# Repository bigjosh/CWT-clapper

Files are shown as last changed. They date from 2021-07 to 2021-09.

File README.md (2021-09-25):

# CWT-CLAPPER firmware, 2021 josh.com


## The mission

Be able to synchonise the clapping of the clappers, which requires sensing when the local clapper last clapped so that it can be positioned for the next clap. This is complicated becuase the only intentional sensor on board is a microphone and it is hard to differentiate beween the sound of a local clap and a nearby clap. 

## Theory of operation 

 1. As the cam rotates and pushes the blade, the spring is progessively streched. 
 2. The farther the spring is streched, the harder it is to strech it further (googgle "Hooke's law"). 
 3. The more force it takes to turn the motor, the more current it uses. 
 4. The more current the motor uses, the lower the voltage across the batteries becomes (google "internal resistance"). 
 5. We can indirectly measure the voltage across the battery with the internal ADC (https://wp.josh.com/2014/11/06/battery-fuel-guage-with-zero-parts-and-zero-pins-on-avr/)
 
 Q.E.D.: We can (sort of, barely, sextuple indirectly) measure the position of the blade by measuring the internal voltage 
 bandgap of the chip using the ADC!
  
 In practice, the change in ADC readings between the blade being fully open and fully shut is very small 
 and there is lots of noise also in these readings.
 
 So we aim to detect the most abupt change in that signal - the moment when the blade claps and the motor goes from pushing 
 a fully streched to spring to not pushing on the blade at all (there is a bit of a dead zone after a clap before the cam
 touches the blade again).
  
 To find this edge, we both filter out high freqnecy noise and amplify the longer running signal by taking periodic ADC samples 
 and summing these over a longer window. We have two consecutive windows, so when we get to the moment where one window is
 filled with samples from before the flap and the other is filled with samples from after the clap, there should be enough SNR to detect
 that by comparing the sums of all the values in each window. 
 
## Demo 
 
See them clap hare....
https://www.youtube.com/watch?v=MOf7x3NkilU&lc=UgzuyXRK9PwrqrHehkx4AaABAg.9SaJbr_eWT19Sc9pGRepJp

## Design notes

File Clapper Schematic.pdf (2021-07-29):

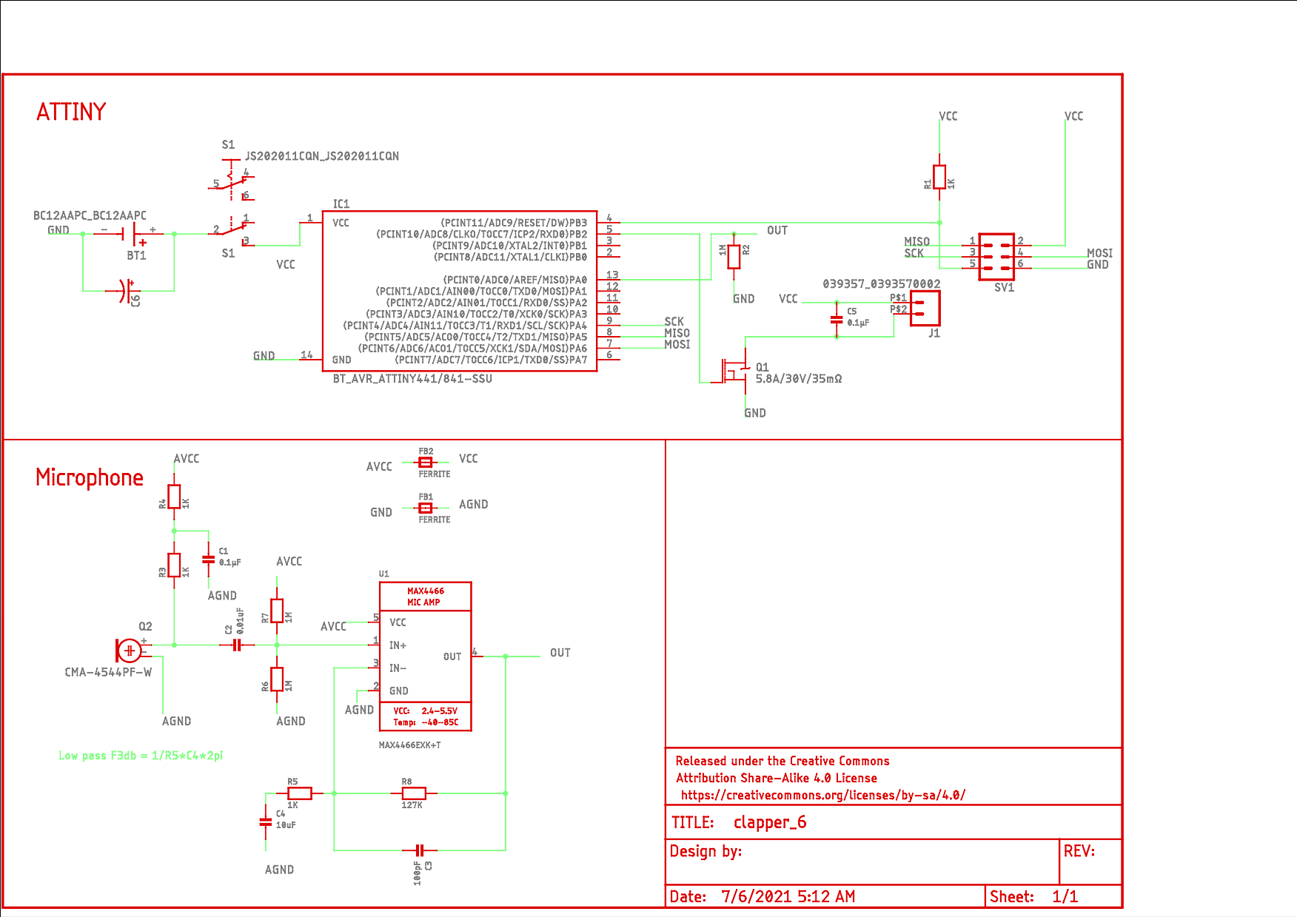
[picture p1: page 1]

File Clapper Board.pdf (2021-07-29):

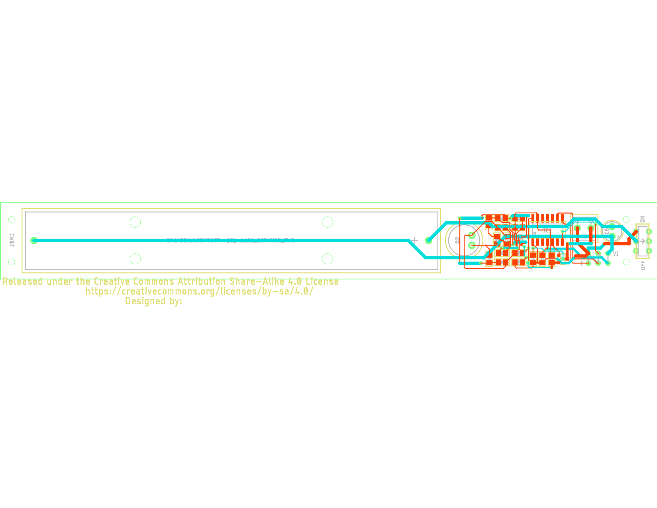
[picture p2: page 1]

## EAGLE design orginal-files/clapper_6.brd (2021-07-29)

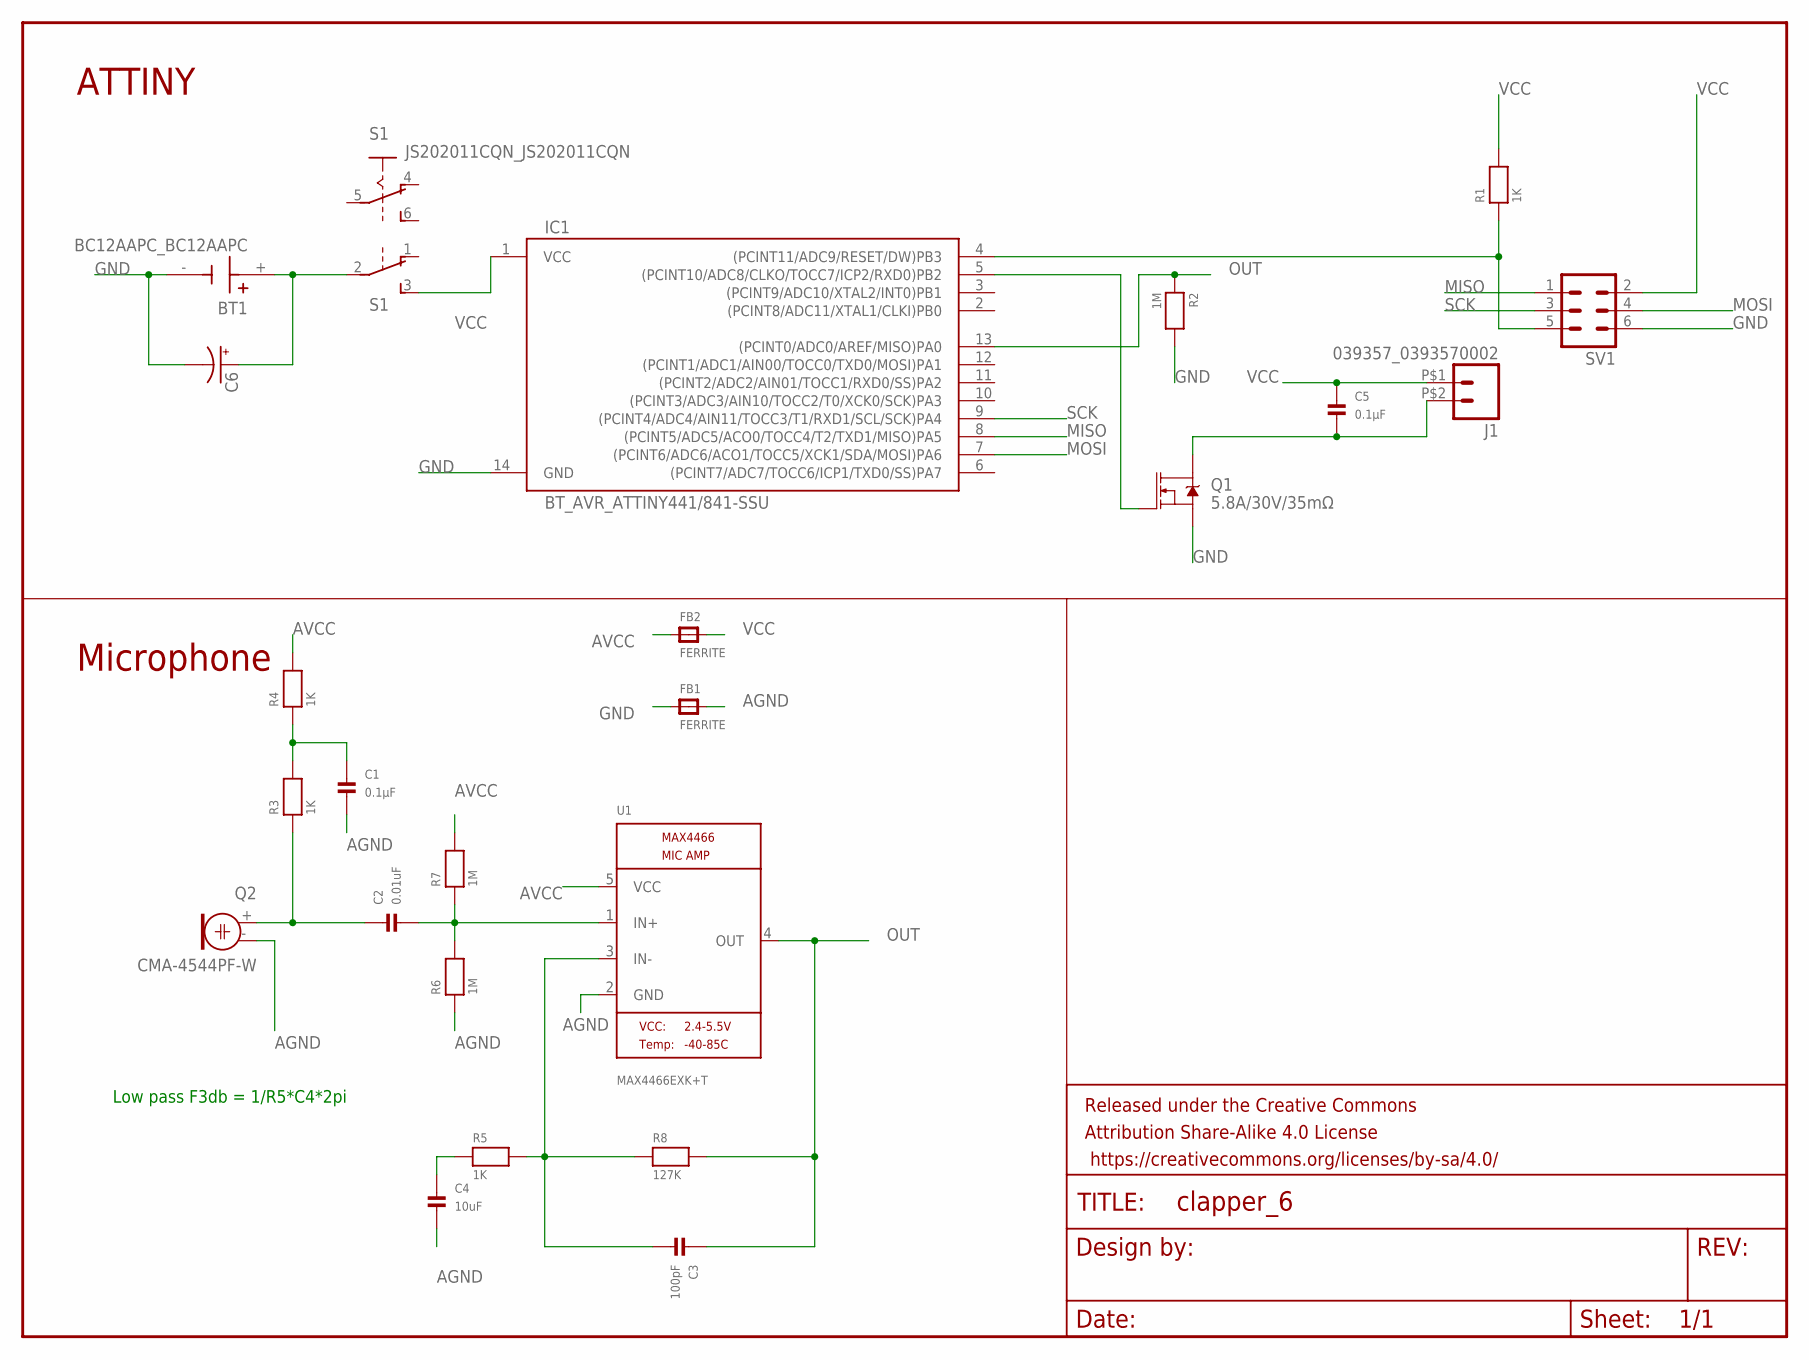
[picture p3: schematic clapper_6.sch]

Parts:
BT1: BC12AAPC_BC12AAPC; BC12AAPC_BAT_BC12AAPC
C1, C5: 0.1µF; MICROBUILDER_0805
C2: 0.01uF; MICROBUILDER_0805
C3: 100pF; MICROBUILDER_0805
C4: 10uF; MICROBUILDER_0805
C6: CPOL-USE2.5-6; E2,5-6
FB1, FB2: FERRITE; MICROBUILDER_0805
FRAME2: FRAME-LETTER; CREATIVE_COMMONS
IC1: BT_AVR_ATTINY441/841-SSU; BT_AVR_SOIC14N
J1: 039357_0393570002
Q1: 5.8A/30V/35mΩ; SOT23-3
Q2: CMA-4544PF-W; MICROBUILDER_ELECTRET_9.7
R1, R3, R4, R5: 1K; MICROBUILDER_0805
R2, R6, R7: 1M; MICROBUILDER_0805
R8: 127K; MICROBUILDER_0805
S1: JS202011CQN_JS202011CQN
SV1: CWT_MA03-2
U1: MAX4466EXK+T; MICROBUILDER_SC70-5

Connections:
AGND: C1.2, C4.2, FB1.2, Q2.- (1), R6.1, U1.2 (GND)
AVCC: FB2.1, R4.2, R7.2, U1.5 (VCC)
GND: BT1.-, C6.-, FB1.1, IC1.14 (GND), Q1.2 (S), R2.2, SV1.6
MISO: IC1.8 ((PCINT5/ADC5/ACO0/TOCC4/T2/TXD1/MISO)PA5), SV1.1
MOSI: IC1.7 ((PCINT6/ADC6/ACO1/TOCC5/XCK1/SDA/MOSI)P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), SV1.4
unnamed: C5.2, J1.P$2 (2), Q1.3 (D)
unnamed: BT1.+, C6.+, S1.2
unnamed: IC1.4 ((PCINT11/ADC9/RESET/DW)PB3), R1.1, SV1.5
unnamed: IC1.5 ((PCINT10/ADC8/CLKO/TOCC7/ICP2/RXD0)PB2), Q1.1 (G)
unnamed: C2.1, Q2.+ (2), R3.1
unnamed: C1.1, R3.2, R4.1
unnamed: C2.2, R6.2, R7.1, U1.1 (IN+)
unnamed: C3.2, R5.2, R8.1, U1.3 (IN-)
unnamed: C4.1, R5.1
OUT: C3.1, IC1.13 ((PCINT0/ADC0/AREF/MISO)PA0), R2.1, R8.2, U1.4 (OUT)
SCK: IC1.9 ((PCINT4/ADC4/AIN11/TOCC3/T1/RXD1/SCL/SC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), SV1.3
VCC: C5.1, FB2.2, IC1.1 (VCC), J1.P$1 (1), R1.2, S1.3 (S), SV1.2

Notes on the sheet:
Low pass F3db = 1/R5*C4*2pi
ATTINY
Microphone

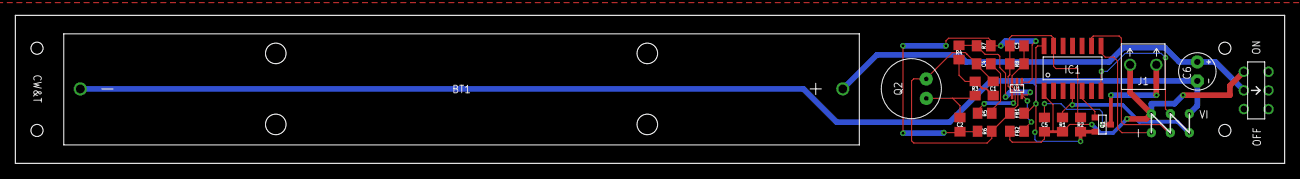
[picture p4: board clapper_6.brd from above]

Board: 2 copper layers, 169.8 x 19.8 mm, 25 parts (0 on the bottom side), 17 nets.

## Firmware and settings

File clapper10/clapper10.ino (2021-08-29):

/*
 * CWT-CLAPPER firmware, 2021 josh.com, https://github.com/bigjosh/CWT-clapper
 * 
 * Theory of operation 
 * ===================
 * 1. As the cam rotates and pushes the blade, the spring is progessively streched. 
 * 2. The farther the spring is streched, the harder it is to strech it further (googgle "Hooke's law"). 
 * 3. The more force it takes to turn the motor, the more current it uses. 
 * 4. The more current the motor uses, the lower the voltage across the batteries becomes (google "internal resistance"). 
 * 5. We can indirectly measure the voltage across the battery with the internal ADC (https://wp.josh.com/2014/11/06/battery-fuel-guage-with-zero-parts-and-zero-pins-on-avr/)
 * 
 * Q.E.D.: We can (sort of, barely, sextuple indirectly) measure the position of the blade by measuring the internal voltage 
 * bandgap of the chip using the ADC!
 * 
 * In practice, the change in ADC readings between the blade being fully open and fully shut is very small 
 * and there is lots of noise also in these readings.
 * 
 * So we aim to detect the most abupt change in that signal - the moment when the blade claps and the motor goes from pushing 
 * a fully streched to spring to not pushing on the blade at all (there is a bit of a dead zone after a clap before the cam
 * touches the blade again).
 * 
 * To find this edge, we both filter out high freqnecy noise and amplify the longer running signal by taking periodic ADC samples 
 * and summing these over a longer window. We have two consecutive windows, so when we get to the moment where one window is
 * filled with samples from before the flap and the other is filled with samples from after the clap, there should be enough SNR to detect
 * that by comparing the sums of all the values in each window. 
 */


// TO COMPLILE AND DOWNLOAD:
//  In Prefs, add to Additional Board URLs: http://drazzy.com/package_drazzy.com_index.json
//  In Board Manager, add: ATTinyCore boards
//  In Tools->Boards menu, select...
//   Board        ->attiny 441/481 (no bootloader)
//   Chip         ->attiny441
//   Clock Source ->8mhz internal <4.5V.
//   Millis       ->Enabled
//   (other stuff doesn't matter)

// After you do this, you should do "Burn Bootloader" at least one time on each chip to set the fuses to the above settings.

#include <avr/pgmspace.h>     // Almost no RAM on this chip, so we keep all strings in flash with `F()`
#include <limits.h>             // Get UNINT_MAX

// Note that all times are in milliseconds

typedef unsigned long millis_t;

// All #defines that start with MOTOR_ concern finding the notch on the cam using the motor current
// All #defines that start with MIC_   concern finding a loud trigger sound using the microphone
// Note that these two kinds of finding are completely independant of each other and only one or the other
// can be happening at any given time. This is good becuase both use the ADC, and we only have one ADC to go around. 

// Number of samples in a window (the are two windows - before- and after-clap)
// More samples mean better filtering and more amplifcation of the small changes, but bigger also means it takes more
// samples (and therefore more time) to detect a change. More samples also needs more memory, which we have very little of. 
const byte MOTOR_WINDOW_SIZE=100;     

// Time between samples. Shorter would be great, but then we would need more memory. The optimal value captures the full drop 
// within one window. Emperically this seems to be about 400ms.
const byte MOTOR_WINDOW_TIME=4;       // Time between samples

// This sets how much the 1st window accumulator must be lower than the 2nd to detect a clap.
// This depends on how much the value changes between pre- and post-clap (very little) times the number of samples in each window.
// Lower values can detect a clap more quickly, but can also lead to false positives. 

const unsigned MOTOR_THRESHOLD=75;

// Number of samples in the mic window looking for loud sounds.
// Grossly speaking, larger window will accept lower freqency sounds.

const unsigned MIC_WINDOW_SIZE=200;

// We need to see a peak-to-peak that is bigger than this within a single sample window to detect a clap sound.
// Bigger numbers mean louder sound needed. 
// Current value taken from orginal clapper software. 

const unsigned MIC_THRESHOLD=550;

// Aim to be this far away from the the edge of the cam when we stop to wait for a trigger.
// Too long means higher latency between when we trigger and when we clap.
// Too short means a greater chance of overshooting and clapping before a trigger and having to go all the way around again. 

// Remember that this includes the time it takes to detect a clap which is about 2 windows, so the minimum time here that will avoid
// premature clapping before preload is MOTOR_WINDOW_SIZE * WINDOW_TIME * 2.


const unsigned POSTLOAD_TARGET_DURRATION=900;

// We turn off the motor for this long immedeately after a clap is detected.
// While this is not required for operation, functionally it serves two purposes...
// Firstly it gives us some external feedback that the clap was accurately detected. Good for troubleshooting.
// Secondly it gives an erie silience (no motors running) after the loud clap, which I quite like. Gives a moment for the clap echos to make an impact.

const unsigned ERIE_SILIENCE_DURRATION=2000;


#define MOTOR_PIN 8     // Motor MOSFET pin

void motorOn(){
  digitalWrite(MOTOR_PIN, HIGH);  
}

void motorOff(){
  digitalWrite(MOTOR_PIN, LOW);  
}

void initMotor() {  
  pinMode( MOTOR_PIN , OUTPUT );
}


// Read only the low 8 bits of the adc. Tosses the highest 2 bits. Usefull to reduce range when the range you are interested happens
// to fall within an 8 bit window. 

byte readADC_low() {

    ADCSRA |= _BV( ADSC );    // Start the conversion    

    while ( ADCSRA &  _BV( ADSC ) );      // Wait for bit to clear (indicates conversion done)

    const uint8_t a = ADCL;                     // Read conversion result. 

    // Note that we toss the high bits of the sample. Our battery voltage range happens to put our readings right in the middle of the ADC low byte range.

    return a;
  
}


unsigned readADC() {

    ADCSRA |= _BV( ADSC );    // Start the conversion    

    while ( ADCSRA &  _BV( ADSC ) );      // Wait for bit to clear (indicates conversion done)

    const unsigned a = ADC;                     // Read conversion result. 

    // Note that we toss the high bits of the sample. Our battery voltage range happens to put our readings right in the middle of the ADC low byte range.

    return a;
  
}


void initADC() {

  ADMUXB = 0x00;          // Against the Vcc

  ADCSRA = 0b10000111;    // Enable ADC, No autotrigger or interrupt, divide by 32 (gives 250Khz @ 8Mhz clock). We are suppoed to be less than 200Khz, but should be ok. 
  
}

void setupADCforMotor() {

  ADMUXA = 0b001101;      // Read the internal 1.1 reference. Datasheet 16.13.1
    
}

void setupADCforMic() {

  // Mic is connected to pin 13, which is ADC0. 

  ADMUXA = 0b00000000;    // Read channel ADC0
  ADMUXB = 0x00;          // Against the Vcc
    
}


// TODO: We are likely very heavily oversampling here. We could instead find the highest freq sound we want to 
// detect and then only sample 2x of that, and do the sampling and threshold checking inside an ISR and sleep between samples. 

bool micCheckForSound() {

  unsigned sample_max = 0;
  unsigned sample_min = UINT_MAX;
  
  for( unsigned window_count = 0 ; window_count < MIC_WINDOW_SIZE; window_count++ ) {
    
    unsigned sample = readADC();
  
    sample_max = max( sample_max , sample );
    sample_min = min( sample_min , sample );
  
    const unsigned peak_to_peak = sample_max - sample_min;   // Note that peak_to_peak will never be negative - lowest it can be here is 0
  
    if ( peak_to_peak >= MIC_THRESHOLD ) {
      return true;
    }  
  
  }
    
 
  return false; 
 
}


byte window1[MOTOR_WINDOW_SIZE];
byte window2[MOTOR_WINDOW_SIZE];

unsigned window1_total=0;
unsigned window2_total=0;

static millis_t next_sample_time = 0; 

// Reset the clap check filter. It will take about 2 windows until another clap can be detected after reset. 
void motorResetPolledClapCheck() {

  next_sample_time = 0; 
  
  window1_total = 0;    
  window2_total = 0;         

  memset( window1 , 0x00 , MOTOR_WINDOW_SIZE ); 
  memset( window2 , 0x00 , MOTOR_WINDOW_SIZE ); 
  
}

// Returns true if a clap is detected
// Call more often than once every WINDOW_TIME

uint8_t motorPolledClapCheck() {

  millis_t now = millis();   // Take an atomic snapshot 

  if (now >= next_sample_time) {

    next_sample_time= now + MOTOR_WINDOW_TIME;     // Do it this way for testing so we can have delay()s in there. 
    
    const byte a=readADC(); 

    const byte window1_pull = window1[MOTOR_WINDOW_SIZE-1];
    window1_total -= window1_pull;
    
    const byte window2_pull = window2[MOTOR_WINDOW_SIZE-1];
    window2_total -= window2_pull;

    // Shift the samples in the windows over. I know a ring buffer would be more efficient, but we don't need efficiency here
    // so keep it simple. 
    for( byte i = (MOTOR_WINDOW_SIZE-1) ; i>0 ; i-- ) {
      window1[i]=window1[i-1];
      window2[i]=window2[i-1];      
    }

    window1[0] = a;
    window1_total += a;
    
    window2[0] = window1_pull;
    window2_total += window1_pull;

    if ( window2_total > window1_total ) {

      const unsigned drop = window2_total - window1_total; 
      
      if (drop >= MOTOR_THRESHOLD) {

        return true;
        
      }
    }
            
  }

  return false;

}


// Delay `delaytime` milliseconds, but return early if a clap is detected while waiting
// Returns ture if clap detected.

uint8_t motorPolledClapCheckDelay( uint16_t delaytime ) {

  millis_t endtime = millis() + delaytime;

  while ( millis() < endtime ) {
    if (motorPolledClapCheck() ) {
      return 1;
    }
  }

  return 0;
  
}


void waitForMicTrigger() {
  
  setupADCforMic();

  while (! micCheckForSound() );

}


// Total motor on time of last clap cycle,

millis_t prevClapCycleDuration=0;   // clap to clap, excluding time waiting for trigger.

void setup()
{

  initADC(); 
  initMotor();
  
  setupADCforMotor(); 

  // On power up we need a baseline for the length of a clap before to drop into our loop
  // so we run a full cycle to time one.

  // Run until we see a clap...
  motorOn();
  motorResetPolledClapCheck();
  while (!motorPolledClapCheck());  

  //Puase for a second to simulate the time we will be waiting for a trigger
  // (Also gives external user indication that we did accurately see the clap)
  motorOff();
  // TODO: Real function that waits to hear a clap to trigger goes here.
  delay(1000);
  motorOn();
    
  motorResetPolledClapCheck();  

  // Time the next clap cycle
  const millis_t start = millis(); 
  while (!motorPolledClapCheck());  
  const millis_t end = millis(); 

  // Calculate the durration.
  prevClapCycleDuration = end - start;

  // OK, we just clapped, motor is running, we have a timed cycle. 
  // We are ready to drop into normal operation...
}

// By convention, loop() is entered immedeiately after a clap has been detected, motor on.

void loop() {

  motorOff();
  delay(ERIE_SILIENCE_DURRATION);    // Breifly turn off the motor after a clap is detected. Not required, but I like it. 
  motorOn();  

  // "preload" is the time we run after a clap to get the cam ready a spot where will we stop and wait for a trigger

  const uint16_t preload_duration = prevClapCycleDuration - POSTLOAD_TARGET_DURRATION;
  
  motorResetPolledClapCheck();

  const millis_t preload_start_time = millis();  // Only used if we clap prematurely to compute the cycle time 
  
  if (motorPolledClapCheckDelay( preload_duration )) {
    
    const millis_t preload_end_time = millis();  // Only used if we clap prematurely to compute the cycle time 
    
    prevClapCycleDuration = preload_end_time  - preload_start_time;    // Adjust to the actual clap cycle time, hopefuly next cycle will be better.
    
    return;
  }

  // We are now at the preload location

  motorOff();
  motorResetPolledClapCheck();
  
  delay(1000);    
  waitForMicTrigger();

  // Triggered. Now run until we detect the clap (should be in about POSTLOAD_TARGET_DURRATION).

  const millis_t postload_start_time = millis();
  motorOn();

  setupADCforMotor();
  while (!motorPolledClapCheck());

  // We just clapped, completing this clap cycle. Compute the time this cycle took so we can be ready for the next one.
  
  const millis_t postload_end_time = millis();

  const millis_t postload_durration = (postload_end_time - postload_start_time);

 // Calculate the total motor run time, which is the combination of the time we spent running to get to the
  // preload position, plus the time we spent running from the preload to the clap (the "post load" time). 

  prevClapCycleDuration = preload_duration + postload_durration;  
  
}
  

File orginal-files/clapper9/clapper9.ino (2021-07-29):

//http://drazzy.com/package_drazzy.com_index.json
//add ATTinyCore boards
//select attiny 441 (no bootloader)
//1mhz internal <4.5V

//add to enable ICE programmer for ATTiny core
//add to programmers.txt file under Library/Arduino15/packages/ATTinyCore/hardware/avr/1.4.1
/*

*/
unsigned int waitTime = 4000; //pause between claps

const int sampleWindow = 20; // Sample window for mic
const float threshold = 550.0; //threshold for neighbor clap
//const float selfThreshold = 999.0234; //threshold for self clap // maxed
const float selfThreshold = 1022; //threshold for self clap // maxed

boolean turnMotorOff;

int cycleCount;

#define MOTOR 8
float selfCount = 0;
unsigned int clap; //clap volume

void setup()
{
  pinMode(MOTOR, OUTPUT);
  turnMotorOff = false;
//    digitalWrite(MOTOR, HIGH);


}

void loop()
{
  unsigned int signalMax = 0;
  unsigned int signalMin = 1024;
  unsigned int signalCount = 0;

  // collect data sample Window
  while (signalCount < sampleWindow)
  {
    clap = analogRead(0);
    if (clap < 1024)  //This is the max of the 10-bit ADC so this loop will include all readings
    {
      if (clap > signalMax) signalMax = clap;  // save just the max levels
      else if (clap < signalMin) signalMin = clap;  // save just the min levels
    }
    signalCount++;
  }

  unsigned int peakToPeak = signalMax - signalMin;  // max - min = peak-peak amplitude
  //float mic = (peakToPeak * 1000.0) / 1024.0;  // convert to percentage
  float mic = peakToPeak;

  //self clap
  if (mic > selfThreshold) {
    turnMotorOff = true;
    selfCount = 0; //reset count
  }

  //neighbor clap
  else if (mic > threshold) {
    if (selfCount <= waitTime) {

      selfCount = 0;

    }
  }

  if (turnMotorOff && selfCount > 10) {
    digitalWrite(MOTOR, LOW);
    turnMotorOff = false;
  }

  if (selfCount > waitTime ) {
    digitalWrite(MOTOR, HIGH);
  }

  selfCount++; //always count up
}

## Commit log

2021-07-10 Triple window filtered samples with hold-off. Seems to work!
2021-07-11 Ready to test detection on wider population!
    Should pause motor for 1 second after each clap.
2021-07-25 Too long, stopping right at the clap. Lets try simplifying...
    [clapper9.ino]
2021-07-29 Re-org files.
    [clapper_6.brd, clapper_6.sch]
2021-08-29 Mictester working
    Does not discriminate between claps and other loud noises, but works well.
    [micTester.ino]
2021-08-29 Rename motor functions to have `motor` in them
    Get ready for `mic` integration.
2021-08-29 It claps.
    Does motor calibration phase then goes into loop where it waits for sound and then claps and starts over.

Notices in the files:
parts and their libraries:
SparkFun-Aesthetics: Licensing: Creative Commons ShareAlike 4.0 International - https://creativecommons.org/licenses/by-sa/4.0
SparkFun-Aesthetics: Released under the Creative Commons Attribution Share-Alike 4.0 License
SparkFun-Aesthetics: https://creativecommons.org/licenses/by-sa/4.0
